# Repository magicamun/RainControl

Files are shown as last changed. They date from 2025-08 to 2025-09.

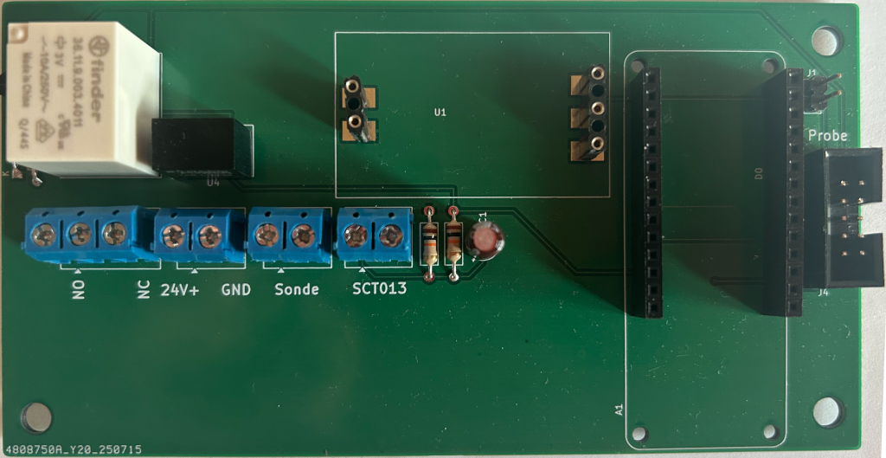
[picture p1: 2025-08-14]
ControllerUnbestückt.png

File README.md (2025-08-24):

# RainControl
Füllstandsmessung einer Zisterne, (Über-)steuerung des Schwimmerschalters der Regenwasserpumpe in Abhängigkeit des Füllstands. 
Messung Strom, Verbrauch der Pumpe, Ableitung an/aus. Anbindung an einen MQTT-Broker zur Werteerfassung und Steuerung

Das Projekt basiert auf der Arbeit aus diesem Repo:

https://github.com/Eisbaeeer/Arduino.Ethernet.Zisterne

Der Nano war aber am Limit was den Speicherplatz angeht und selbst kleinste Optimierungen führten zu zu großen Images oder liefen im Betrieb instabil,
daher habe ich das Projekt auf anderer Hardware aufgesetzt. Zugegeben - das ist jetzt deutlich teurer aber macht so auch mehr Spaß (finde ich).
Ich benötige mangels stabilem WLAN im Technikraum Ethernet - daher das Shield.

Hardware:
  [Arduino MKR Zero](https://store.arduino.cc/collections/mkr-family/products/arduino-mkr-zero-i2s-bus-sd-for-sound-music-digital-audio-data) 
  
  [MKR Ethernet-Shield](https://store.arduino.cc/collections/mkr-family/products/arduino-mkr-eth-shield) - Zur Anbindung an eine Hausatomation, bzw. an einen MQTT-Broker (IOBroker)
  
  Pegelsonde zur Messung des Füllstands mittels Druck - Voraussetzung zur korrekten Füllstandsermittlung ist ein Höhensymmetrisches Volumen (aufrecht stehender Zylinder, Quader), Liegende Zylinderformen sind nicht geeignet. Z.B. so eine hier:
  
  [Füllstandssensor Pegelsensor Drucksensor Wasserstandsensor 4-20mA 0-5m DE](https://www.ebay.de/itm/177255784278?itemid=177255784278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)
  
  [Stromsensor SCT013 - 5A, 1V](https://www.amazon.de/HUABAN-Nicht-invasiver-Split-Core-Stromwandlersensor/dp/B089FNQ5GX?th=1)

  [Steckernetzteil 24V DC](https://www.conrad.de/de/p/dehner-elektronik-saw-30-240-1000g-steckernetzteil-festspannung-24-v-dc-1000-ma-24-w-1549855.html)

Bauteile für die Schaltung, Platine
  
  Controller
  - [Spannungswandler TSR-1 2433 (Wandlung Eingangsspannung 24V auf 3,3V](https://www.conrad.de/de/p/tracopower-tsr-1-2433-dc-dc-wandler-print-24-v-dc-3-3-v-dc-1-a-75-w-anzahl-ausgaenge-1-x-inhalt-1-st-156671.html) zur Versorgung der Schaltung mit 3,3V
  - [Strom/Spannungswandler](https://de.aliexpress.com/item/1005001604138590.html) zur Wandlung des Stroms der Sonde in Spannung inkl. Kalibrierung von 0-Punkt und Maximum
  - [Relais Finder 36.11 Schaltspannung 3V](https://www.conrad.de/de/p/finder-36-11-9-003-4011-printrelais-3-v-dc-10-a-1-wechsler-1-st-3323202.html)
  - [Steckerleisten 14 polig](https://www.conrad.de/de/p/econ-connect-buchsenleiste-standard-anzahl-reihen-1-polzahl-je-reihe-14-blg1x14-1-st-1492306.html)
  - [Transistor BC337](https://www.conrad.de/de/p/diotec-transistor-bjt-diskret-bc337-25-to-92-anzahl-kanaele-1-npn-155900.html) zur Schaltung von Relais und LED
  - D1 [Diode (1N 4148)](https://www.conrad.de/de/p/diotec-ultraschnelle-si-diode-1n4148-sod-27-75-v-150-ma-162280.html)
  - R1 [1x Widerstand 330 Ohm](https://www.conrad.de/de/p/yageo-cfr25j330rh-cfr-25jt-52-330r-kohleschicht-widerstand-330-axial-bedrahtet-0207-0-25-w-5-1-st-1417730.html)
  - R2, R3 [2x Widerstand 10k Ohm](https://www.conrad.de/de/p/yageo-cfr25j10kh-cfr-25jt-52-10k-kohleschicht-widerstand-10-k-axial-bedrahtet-0207-0-25-w-5-1-st-1417697.html)
  - [10uF Elko](https://www.conrad.de/de/p/frolyt-e-rf3058-elektrolyt-kondensator-radial-bedrahtet-2-5-mm-10-f-16-v-20-o-x-l-5-mm-x-12-mm-1-st-3046377.html)
  - 3 x [Schraubklemmblock 2 polig](https://www.conrad.de/de/p/deca-1216197-schraubklemmblock-1-50-mm-polzahl-3-blau-1-st-1216197.html) (Sonde Zisterne, Spannungsversorgung 24V, Stromsensor SCT 013)
  - 1 x [Schraubklemmblock 3-polig](https://www.conrad.de/de/p/deca-1282826-schraubklemmblock-1-50-mm-polzahl-2-blau-1-st-1282826.html) (Umschaltung Regenwasserpumpe, Übersteuerung Schwimmerschaltung - ACHTUNG - 230V)
  
  Displaypanel
  - R1 [1x Widerstand 390 Ohm](https://www.conrad.de/de/p/yageo-mf0207f390rh-mf0207fte52-390r-metallschicht-widerstand-390-axial-bedrahtet-0207-0-6-w-1-1-st-1417596.html)
  - [LED - Rot, 3mm](https://www.conrad.de/de/p/quadrios-2111o155-led-bedrahtet-rot-rund-3-mm-700-mcd-30-20-ma-2-v-2583896.html)
  - [2 Taster (Reset und Mode)](https://www.conrad.de/de/p/weltron-t604-t604-drucktaster-24-v-dc-0-05-a-1-x-aus-ein-tastend-l-x-b-x-h-6-x-6-x-9-5-mm-1-st-700479.html)
  Display
  - [2,42" 128X64-OLED-Anzeigemodul SPI - 2.42 Zoll OLED Bildschirm kompatibel mit Arduino UNO R3 - Weiße Schrift OLED :](https://www.az-delivery.de/products/oled-2-4-white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)

  Zur Verbindung von Controllerplatine mit der Displayplatine:
  
  2 x [Wannenstecker 8polig](https://www.conrad.de/de/p/bkl-electronic-10120552-stiftleiste-ohne-auswurfhebel-rastermass-2-54-mm-polzahl-gesamt-8-anzahl-reihen-2-1-st-741552.html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)
  
  2 x [Pfostensteckverbinder mit Zugentlastung](https://www.conrad.de/de/p/tru-components-1580952-pfosten-steckverbinder-mit-zugentlastung-rastermass-2-54-mm-polzahl-gesamt-8-anzahl-reihen-2-1-1580952.html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)
  
  1 x [Flachbandkabel 8 polig](https://www.conrad.de/de/p/econ-connect-28awg8gr-flachbandkabel-rastermass-1-27-mm-8-x-0-08-mm-grau-30-50-m-1656444.html)

  Sonstiges Material:
  - Bopla Gehäuse](https://www.conrad.de/de/p/bopla-euromas-m-231-02231000-industrie-gehaeuse-160-x-80-x-85-polycarbonat-lichtgrau-ral-7035-1-st-531785.html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)
  - [Passende Einbaubuchse für das Netzteil](https://www.conrad.de/de/p/cliff-scd-026-niedervolt-steckverbinder-buchse-einbau-vertikal-5-5-mm-2-1-mm-1-st-735640.html)
  - [Einbaubuchse für Klinkenstecker vom SCT013](https://www.conrad.de/de/p/tru-components-718574-klinken-steckverbinder-3-5-mm-buchse-einbau-vertikal-polzahl-3-stereo-schwarz-1-st-1564526.html)
    
Das Platinenlyout wurde mit KiCad in 2 Projekten erstellt - eines für das Display, eines für den Controller.

Funktionsweise technisch:

Füllstandsmessung:
  Die Sonde wird mit 24V betrieben und da bietet sich ein Netzteil handelsüblich an und eine Spannungswandlung (TSR-1 2433) von den 24V DC auf 3,3V für den Rest der Schaltung (Arduino MKR Zero, Relais, Display).
  Die Sonde liefert einen Strom in Abhängigkeit vom Druck (Füllstandshöhe). Der Wandler macht aus dem Strom eine Ausgangsspannung von 0 bis Vmax (3,3V).
  Diese Spannung wird am A0 (AnalogInput 0) des Arduino erfasst und in einen Füllstand umgerechnet - der Füllstand (Volumen) ist proportional zum gemessenen Wert an A0.
  Voraussetzung ist ein Behälter, dessen Füllstand (Volumen) sich linear proportional zum Druck verhält (Senkrechter Zylinder).
  
  Der Wandler für den Messwert an A0 muss vor Inbetriebnahme des Systems kalibiriert werden.
  ACHTUNG: Die Kalibrierung muss im ersten Schritt grob ohne angeschlossenen Arduino erfolgen um Beschädigungen durch Überspannung am Eingang des Arduino zu vermeiden.
  -> Siehe Kalibrierung und Inbetriebnahme.
  
  In Abhängigkeit von der gemessenen Füllhöhe und zwei einzustellenden Werten (LimitLow, LimitHigh) schaltet der Arduino das Relais sowie eine LED über PIN D14 an oder aus.
  Damit bei unterem Schwellwert / Minimum nicht sofort bei erneutem überschreiten (Nachlauf Regen) wieder zurück geschaltet wird, gibt es einen weiteren Wert (Oberer Schwellwert),
  der erreicht werden muss, damkt zurück auf Zisterne geschaltet wird.

Strom, Pumpe an oder aus:
  Über den Stromsensor SCT013 kann der Zustand der Pumpe (Regenwassernutzung) abgefragt werden, ohne in die Anlage eingreifen zu müssen.
  Dazu wird der Stromsensor unter der Beachtung der Stromflussrichtung um die Phase (nur die Phase) zur Pumpe gelegt.
  Am Ausgang des Sensors wird über Induktion eine Wechselspannung abgegeben. Dabei sind die Werte des Sensors zur korrekten Berechnung des Stroms und der Leistung in der Software einzustellen.
   Wichtig ist eine korrekte Dimensionierung des Sensors - es gibt unterschiedliche Typen. Für eine möglichst feine Auflösung ist der Messbereich (Ampere) des Sensors möglichst klein zu wählen, 
   aber groß genug, dass bei Vollast der Pumpe der Wert der Leistung ausreicht. Der hier benutzte Sensor misst bis 5A -> 1,1kw. Meine Pumpe hat 800 Watt Leistungsaufnahme.
   Gleichzeitig soll der Sensor möglichst große Spannungswerte am Ausgang produzieren, damit die Auflösung des Wertes möglichst fein/genau ist.
   Es gibt die Sensoren mit 0,33V und 1V Ausgangsspannung -> ich nutze hier 1V. Da die Spannung eine Wechselspannung ist, wird über den Spannungsteiler am Sensor die Wechselspannung um +1,65V angehoben.
   Der analoge Wert an A1 wird in einen Wert für den Stromverbrauch umgerechnt. Dazu ist es wichtig, den Messbereich des Sensors, die Ausgangsspannung des Sensors und den Referenzwert am Arduino (Zero 3,3V)
   zu kennen und in der Software einzustellen.

Am Pin D13 ist ein Taster von der Displayplatine angeschlossen, mit dem der Betriebsmodus der Steuerung manuell gesetzt werden kann:
  - Auto - Der Arduino übernimmt die Ventilsteuerung (Relais und Ansteuerung Schwimmerschalter der Pumpe) in abhängigkeit des Füllstandes
  -   Füllstand < LimitLow -> Relais auf "Hauswasser"
  -   Füllstand > LimitHigh -> Relais auf "Zisterne"
  -   Wenn der Füllstand kleiner als LimitLow war und immernoch kleiner als LimitHigh ist -> Ventil auf Hauswasser
  - Manuell Zisterne -> Relais auf "Zisterne"
  - Manuell Hauswasser -> Relais auf "Hauswasser"

  Per Tasterdruck wird zyklisch durch die Betriuebsmodi geschaltet, wobei die tatsächliche Umschaltung erst nach 10Sekunden ohne erneute Tasterbetätigung erfolgt

Das Display zeigt Datum, Uhrzeit, Füllstand und Betriebsmodus an

Mit dem an RST angeschlossenen Taster lässt sich der Controller resetten.

Ventilsteuerung generell:
Der Controller misst den Füllstand und (kann) in Abhängigkeit davon einen Schwimmerschalter für handelsübliche Zisternenpumpen ersetzen. Dazu ist die Steuerung der Pumpe auf "Automatik" zu stellen
und statt des Schwimmerschalters ein 230V - Kabel vom Anschluss des Schwimmerschalters zum Controller (3 - polige Klemme) zu führen.
Am Schraubklemmenblock 3 polig ist in jedem der mittlere Anschluss zu belegen und dann entweder NO (Normally open) oder NC (normally connected) - sonst schaltet am Ventil der Regenwasserpump nichts.

Funktionsweise Software:

Sämtliche Systemzustände werden bei Veränderung alle Sekunde an einen MQTT-Broker gesendet, spätestens alle 30 Sekunden auch unverändert. Das System führt folgende Werte:

- Booted     -> Boot-Zeitpunkt
- Timestamp  (Datum, Uhrzeit)
- Uptime     -> Zeit seit l. Boot/Neustart
- Mode       (0 = Zisterne, 1 = Hauswasser, 2 = Auto) -> Betriebsmodus
- Modus      -> Modus als Text
- Valve      (0 = Zisterne, 1 = Hauswasser) -> Ventilstellung
- Ventil     -> Ventilstellung als Text ("Zisterne", "Hauswasser")
- Reason     -> Grund für Ventilstellung (0 = "Manuell", 1 = "Zisterne voll", 2 = "Zisterne leer")
- Reasontext -> Reason als Text
- AnalogMin  -> Mindestwert, den die Sonde liefern muss, damit Sonde als vorhanden erkannt wird
- AnalogMax  -> Maximaler analoger Wert an A0 für volle Zisterne
- Analog     (0-1023) -> Analoger Messwert der Pegelsonde (0-1023)
- Liter      -> Füllung in Liter
- Prozent    -> Füllstand in %
- LimitLow   -> Unterer Schwellwert in Liter
- LimitHigh  -> Oberer Schwellwert in Liter
- LiterMin   -> Restfüllstand bei "leer" - unterer Grenzwert -> AnalogMin.
- LiterMax   -> maximales Füllvolumen wird benötigt zur Umrechnung des analogen Wertes in Liter (Analog = LiterMax / AnalogMax)
- StatusSonde-> Ist eine Sonde korrekt angeschlosen (Wenn der Analoge Wert unter einem Minimum liegt, dann ist davon auszugehen, dass die Sonde nicht korrekt angeschlossen ist
- HyaRain    -> Pumpe läuft (ON), oder nicht (OFF)
- Current    -> Stromverbrauch in Ampere
- Power      -> Watt (Volt * Leistung pro Sekunde
- KWh        -> KLilowattstunden

Es gilt:
LiterMin <= LimitLow <= LimitHigh <= LiterMax
Bei mir mit 6500l Zisterne und Restmenge von knapp 500l: 
LiterMin = 500, LimitLow = 600, LimitHigh = 1000, LiterMax = 6500. Bei unterschreiten von 600l schaltet das Relais auf Hauswassernachspeisung,
sobald wieder mehr als 1000l in der Zisterne sind, wird zurück auf Zisterne geschaltet.

Per MQTT kann der Controller aber auch gesteuert werden:
 - cmd/Mode [0,1,2,Hauswasser,Zisterne,Auto] -> Es kann der Modus umgestellt werden (nicht nur per Taster)
 - cmd/Limit [low|high]=<Number> -> Einstellen der Schwellwerte 
 - cmd/Calibrate [analogmin|analogmax|litermax]=<number> -> Einstellen der Kalibrierung in der Software nach dem die Sonde und der Wandler kalibriert wurden

Bei eingelegter SD-Card werden die Daten über einen Reset hinaus auf der SD-Card gespeichert und nach Neustart gelesen.
Wenn man darauf verzichtet die Werte nach dem Aufspielen der Software und der Einstellung in der Software zu verändern ist eine SD-Card nicht nötig

Aufbau, Inbetriebnahme
1. Platinenlayout, Produktion der Platinen
  Im Repository sind in den Unterordnern Controller und Displaypanel je ein KiCad-Projekt mit dem Schema und dem Platinenlayout - wer mag, kann damit andere Platinenformate erzeugen
  oder aber die Schaltung anpassen.
  Die zwei Zip-Archive im Hauptverzeichnis enthalten die Gerberdateien um PCB's produzieren zu lassen. [JLCPCB](https://jlcpcb.com) hat mir gute Dienste geleistet. Der Preis für jeweils 5 Stück (kleinste Einheit) Controler und 
  Display liegt bei 13.50$US - zzgl Versand, Zoll ist man dann bei knapp 30$. Lieferzeit etwa 1 Woche (je nach Zollabfertigung und lokalem Shipment)

2. Aufbau der Platine
  Die Platinen mit den Bauteilen bestücken. Dabei mit den flachen anfangen (Widerstände, Diode, Transistor), dann Buchsenleisten, Schraubklemmenblöcke, Relais, Spannungswandler

  Nach dem Zusammenbau, der Bestückung der Platine erfolgt schrittweise die Inbetriebnahme - noch ohne Arduino und ohne den Strom/Spannungswandler.
  Buchsenleisten sind nützlich für den Arduino (quasi ein muss) und für den Strom-/Spannungswandler. 
  Den Strom/Spannungswandler befreie ich von den Schraubklemmen (auslöten) und ersetze die durch Stiftleisten - einfacher Tausch.
  Dazu bekommt die Platine je Gegenstück eine Buchsenleiste 2 polig und 3 polig mit 5er Raster.

  Bei der Displayplatine darauf achten, dass der Wannenstecker auf die Rückseite kommt und die Polung korrekt ist - siehe Bilder

3. Prüfung der Spannungen
   An Pin 3 des Strom/Spannungswandlers müssen 24V anliegen (auf dem Board rechte Buchsenleiste oberer Pin/Buchse)
   Am Schraubklemmenblock für die Sonde müssen 24V anliegen
   Am Pin 3 der Stiftleiste für den Arduino müssen gegenüber GND (Pin 4) 3,3Volt anliegen

3. Einstellen des Strom/Spannungswandlers (idealerweise bei voller Zisterne)
   Erster Durchgang des Einstellens OHNE Arduino
      Zum Einstellen des Stromspannungswandlers wird selbiger in die Buchsenleisten gesteckt. Ebenso wird an der Stiftleiste "Probe" ein Multimeter zur Spannungsmessung angeschlossen.
      Ohne Sonde liefert das Multimeter dann 0V. Dann wird die Sonde angeschlossen und noch nicht in die Zisterne herabgelasse. Es erfolgt die Nullpunkteinstellung für "leer".
      Mit dem linken Poti dreht man jetzt solange nach links (kleiner) oder nach rechts (größer), bis die gemessene Spannung verlässlich nah an 0V liegt aber eben noch größer als 0V ist.
      Jetzt kann die Sonde in die Zisterne gelassen werden - so tief wie möglich. Zur korrekten Kalibrierung des Maximalwertes ist es am einfachsten den maximalen Füllstand auch zur Einstellung
      der maximalen Spannung zu nutzen. Dazu dreht man jetzt am rechten Poti des Wandlers (links kleiner, rechts größer) bis die gemessene Spannung nah bei 3,3V ist. Es empfiehlt sich etwas "Luft" zu lassen.
   Zweiter Durchgang mit Arduino - die Werte sind verändert, die Vorgehensweise ist die gleiche
      Wichtig ist jetzt, dass jetzt die Analogen Messwerte angeschaut werden.
      Messwert 1 "Sonde angeschlossen, aber nicht unter Druck" -> Dies wird mit dem Poti links auf einen möglichst kleinen aber stabil kleinen Wert über Null eingestellt (bei mir 50).
      Dieser Wert wird in der Software im #DEFINE ANALOG_MIN abgelegt.
      Messwert 2 "Sonde angeschlossen und Maximaler Füllstand der Zisterne und Sonde am tiefsten Punkt (maximaler Druck)
      Den Messwert stellen wir mit dem rechten Poti so ein, dass er möglichst groß ist (nah an 1023), aber noch etwas Luft ist, falls die Zisterne mal "übervoll" ist - Mehr Zulauf als Ablauf (kommt schonmal vor bei mir)
      Den Wert dann in #DEFINE ANALOG_MAX ablegen.
      Die Defines für LITER_MIN mit einem Wert für die Restmenge in der Zisterne bevor die Pumpe auf Störung laufen würde (bei mir sind dann noch 15cm in der Zisterne drin und damit rund 470 Liter.
      LITER_MAX einstellen mit dem maximalen regulären Füllvolumen der Zisterne.

   Wenn die Zisterne nicht voll ist, sollte man abschätzen können, wie voll (in Prozent) sie ist, man kann dann ausgehend vom Zielwert bei "Zisterne Voll" nah bei 3,3V und
   dem unteren Messwert für "leer" den Spannungswert, den man jetzt messen möchte im Dreisatz ableiten und dann einstellen am Poti.
4. Aufspielen der Software auf den Arduino
5. Board stromlos machen / Spannungsversorgung trennen
6. Aufstecken des Arduino und des Ethernet-Shields auf die Buchsenleisten 14 polig
7. Verbinden des Displays mit dem Controller (Wenn das Display NICHT angeschlossen ist, dann wird der Arduino NICHTS tun.)
8. Netzteil anschließen
9. Der Arduino bootet und auf dem Display werden die Daten angezeigt
10. Die Daten werden zyklisch an den MQTT-Broker verteilt (Bei Änderungen sekündlich, ansonsten alle 30 Sekunden)
11. Prüfung der Messwerte am Broker
12. Es empfiehlt sich, dass nach ein paar Wochen Betrieb und Leer, Voll-Zyklen nochmal die Messwerte der Kalibrierung geprüft werden und notfalls nochmal in der Software neu eingestellt werden - entweder per MQTT oder "hart" per Software

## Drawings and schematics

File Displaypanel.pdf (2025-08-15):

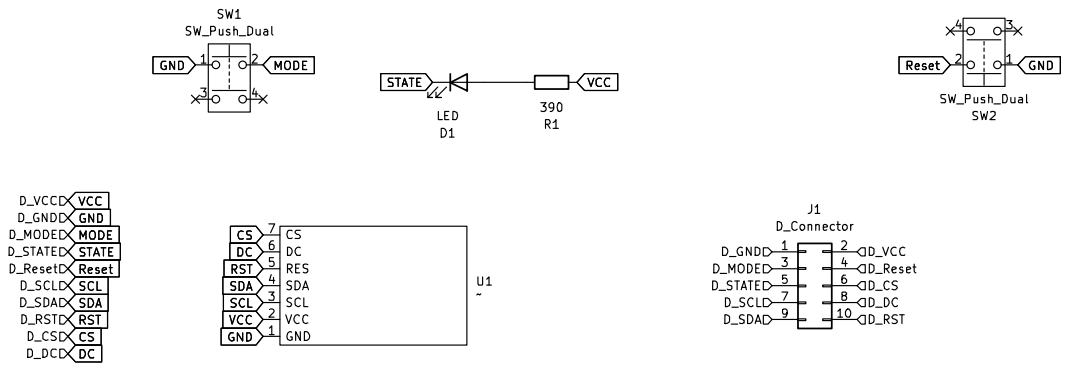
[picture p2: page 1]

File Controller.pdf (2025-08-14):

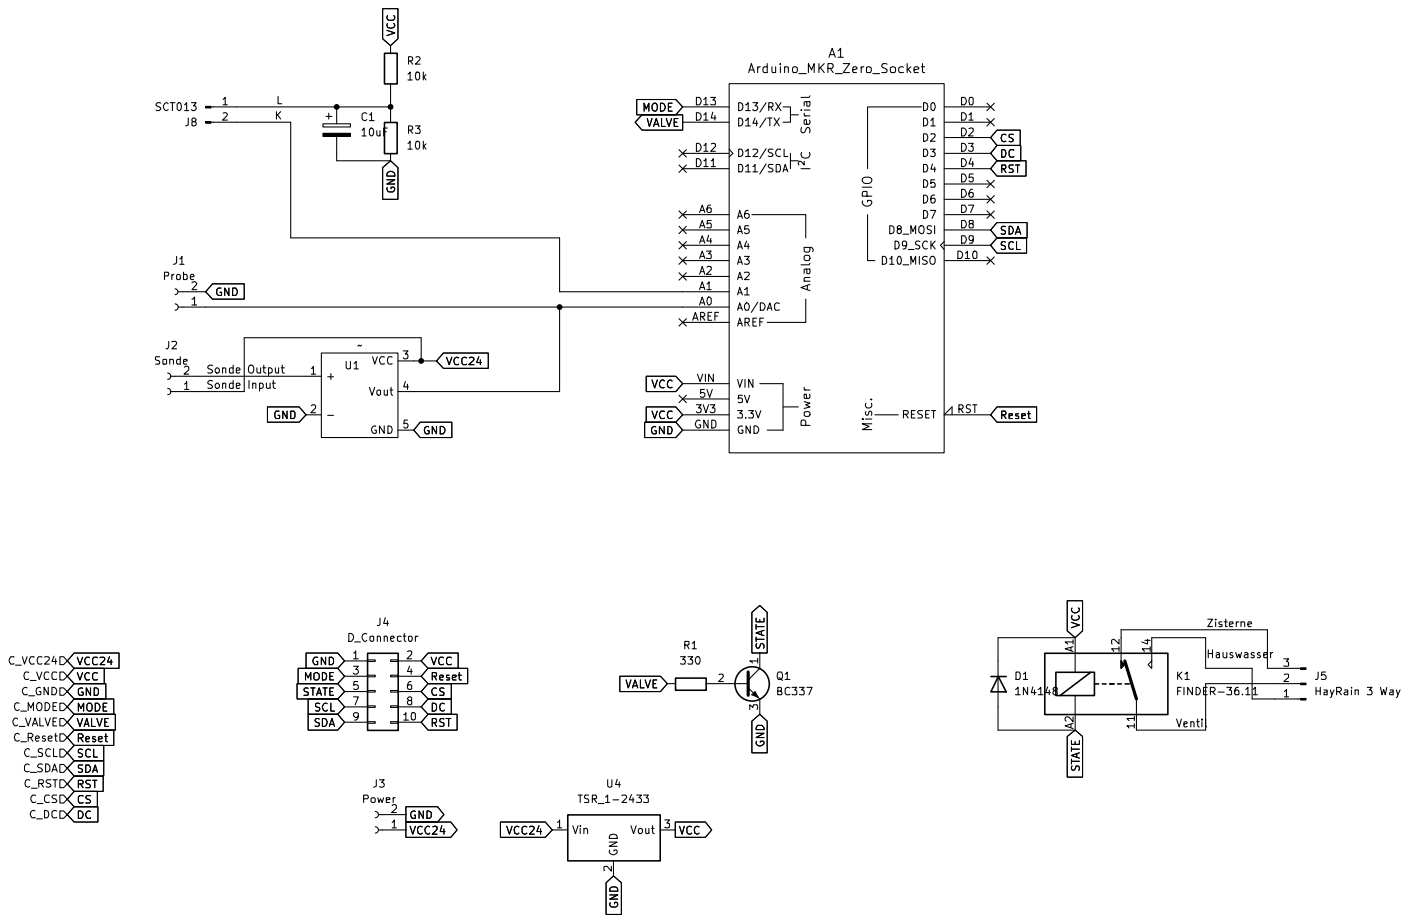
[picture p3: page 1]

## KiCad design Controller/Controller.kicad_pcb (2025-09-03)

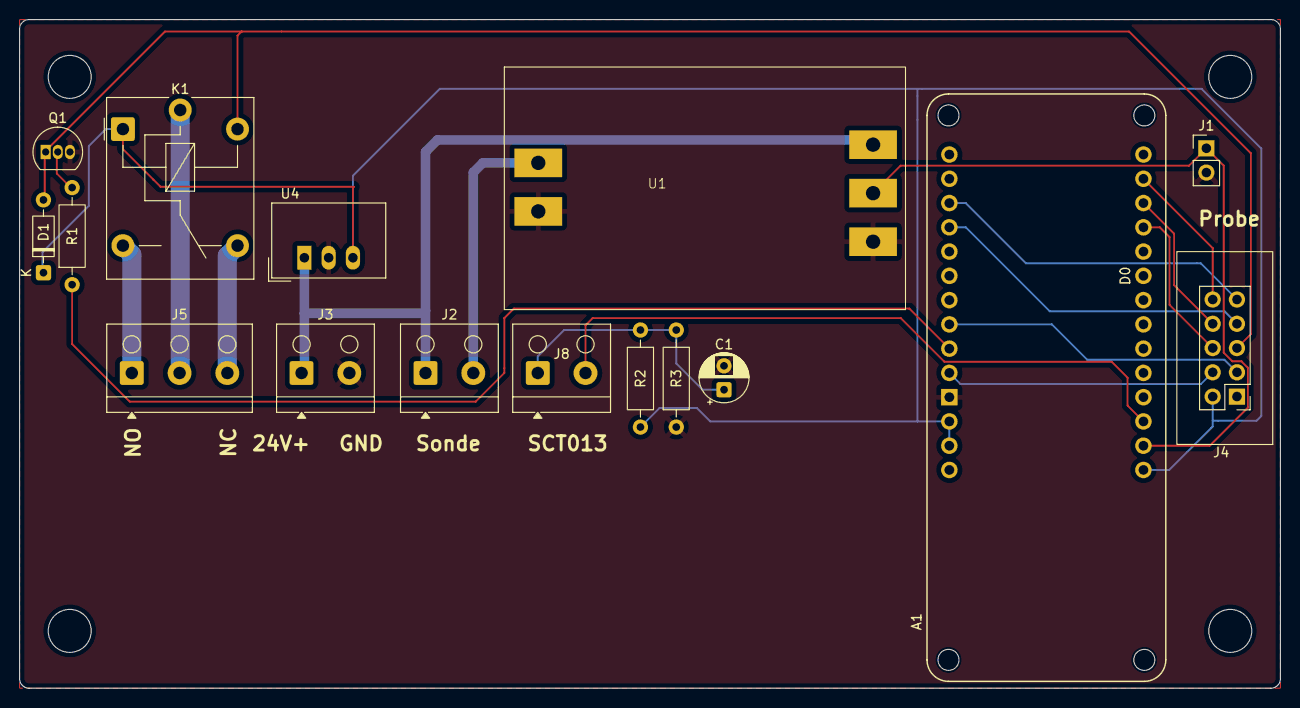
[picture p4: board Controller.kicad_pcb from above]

Board: 2 copper layers, 132.0 x 70.0 mm, 16 parts (0 on the bottom side), 20 nets.

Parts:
A1: Arduino_MKR_Zero_Socket
C1: 10uF; CP_Radial_D5.0mm_P2.50mm
D1: 1N4148; D_DO-35_SOD27_P7.62mm_Horizontal
J1: Probe; PinHeader_1x02_P2.54mm_Vertical
J2: Sonde; TerminalBlock_RND_205-00001_1x02_P5.00mm_Horizontal
J3: Power; TerminalBlock_RND_205-00001_1x02_P5.00mm_Horizontal
J4: D_Connector; WSL 10G
J5: HayRain 3 Way; TerminalBlock_RND_205-00002_1x03_P5.00mm_Horizontal
J8: SCT013; TerminalBlock_RND_205-00001_1x02_P5.00mm_Horizontal
K1: FINDER-36.11; Relay_SPDT_Finder_36.11
Q1: BC337; TO-92_Inline
R1: 330; R_Axial_DIN0207_L6.3mm_D2.5mm_P10.16mm_Horizontal
R2, R3: 10k; R_Axial_DIN0207_L6.3mm_D2.5mm_P10.16mm_Horizontal
U1: Konverter
U4: TSR_1-2433; Converter_DCDC_TRACO_TSR-1_THT

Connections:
/Hauswasser: J5.1, K1.14
/K: A1.A1, J8.2
/L: C1.1, J8.1, R2.1, R3.2
/Sonde Output: J2.2, U1.1 (+)
/Ventil: J5.2, K1.11
/Zisterne: J5.3, K1.12
CS: A1.D2, J4.6
DC: A1.D3, J4.8
GND: A1.GND, C1.2, J1.2, J3.2, J4.1, Q1.3 (E), R3.1, U1.2 (-), U1.5 (GND), U4.2 (GND)
MODE: A1.D13 (D13/RX), J4.3
unnamed: A1.A0 (A0/DAC), J1.1, U1.4 (Vout)
unnamed: Q1.2 (B), R1.2
RST: A1.D4, J4.10
Reset: A1.RST (RESET), J4.4
SCL: A1.D9 (D9_SCK), J4.7
SDA: A1.D8 (D8_MOSI), J4.9
STATE: D1.2 (A), J4.5, K1.A2, Q1.1 (C)
VALVE: A1.D14 (D14/TX), R1.1
VCC: A1.3V3 (3.3V), A1.AREF, A1.VIN, D1.1 (K), J4.2, K1.A1, R2.2, U4.3 (Vout)
VCC24: J2.1, J3.1, U1.3 (VCC), U4.1 (Vin)

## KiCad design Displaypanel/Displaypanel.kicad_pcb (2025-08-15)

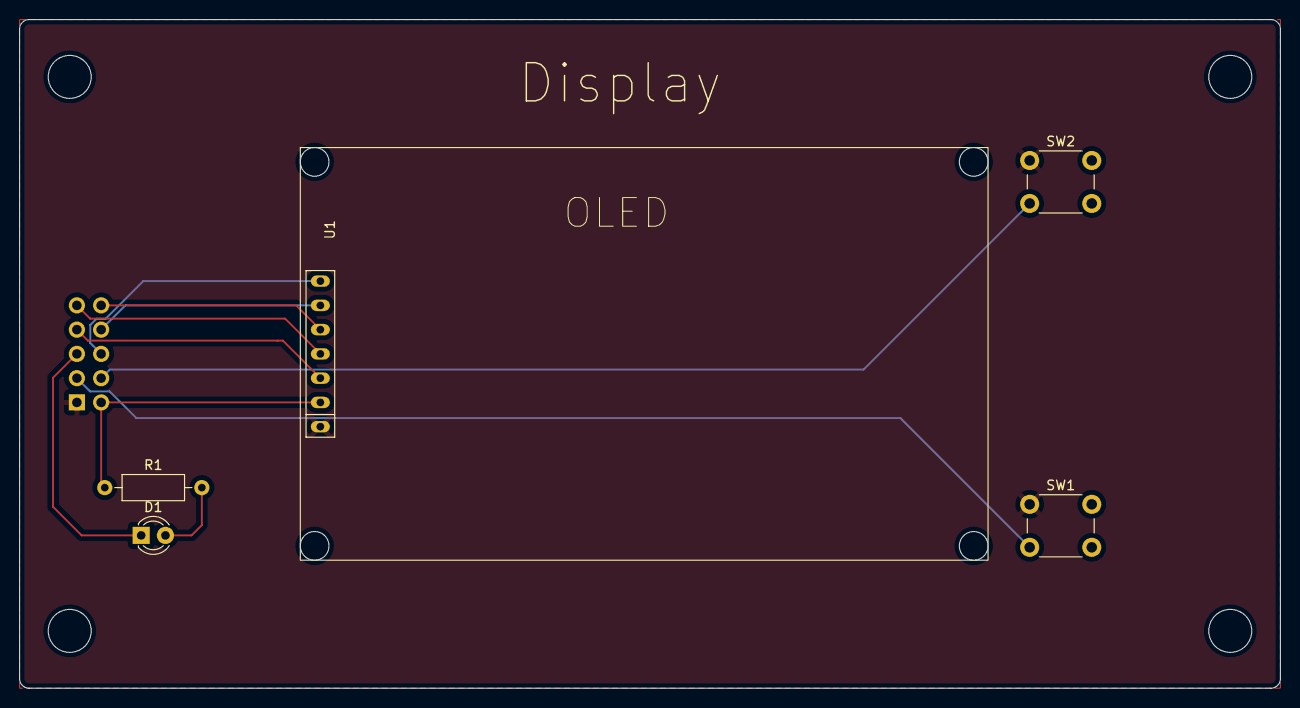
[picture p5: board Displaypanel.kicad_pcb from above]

Board: 2 copper layers, 132.0 x 70.0 mm, 6 parts (1 on the bottom side), 11 nets.

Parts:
D1: LED; LED_D3.0mm_Clear
J1: D_Connector; WSL 10G
R1: 390; R_Axial_DIN0207_L6.3mm_D2.5mm_P10.16mm_Horizontal
SW1, SW2: SW_Push_Dual; SW_PUSH_6mm_H4.3mm
U1: OLED 128x64 SPI

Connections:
CS: J1.6, U1.7 (CS)
DC: J1.8, U1.6 (DC)
GND: J1.1, SW1.1, SW2.1, U1.1 (GND)
MODE: J1.3, SW1.2
unnamed: D1.2 (A), R1.2
RST: J1.10, U1.5 (RES)
Reset: J1.4, SW2.2
SCL: J1.7, U1.3 (SCL)
SDA: J1.9, U1.4 (SDA)
STATE: D1.1 (K), J1.5
VCC: J1.2, R1.1, U1.2 (VCC)

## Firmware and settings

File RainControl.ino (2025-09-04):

#include <Arduino.h>
#include <avr/dtostrf.h>
#include <PubSubClient.h>
#include <Time.h>
#include <Ethernet.h>
EthernetClient ethClient;

#include <EthernetUdp.h>
EthernetUDP Udp;

#include <MyNTP.h>
MyNTP ntp(Udp);

#include <SD.h>
#include <U8g2lib.h>
U8G2_SSD1309_128X64_NONAME2_F_4W_HW_SPI u8g2(U8G2_R0, /* cs=*/ 2, /* dc=*/ 3, /* reset=*/ 4);

#ifdef U8X8_HAVE_HW_SPI
#include <SPI.h>
#endif
#ifdef U8X8_HAVE_HW_I2C
#include <Wire.h>
#endif

/* ---------------------------- allgemeine Settings ----------------------------- */
#define VERSION "RainControl V1.0"

// For Debugging with no Display connected, comment out for real-world
#define HAS_DISPLAY
// Minimize Serial Output
// #define DEBUG
// ##############################################################################################################################
// ---- HIER die Initialen Einstellungen vornehmen, die Werte sind über MQTT anpassbar
// ##############################################################################################################################
// Hier die maximale Füllmenge des Behälters angeben. Dies gilt nur für symmetrische Behälter.
// Deckelung bei 100%
// keine Deckelung bei "Übervoll", sondern Max-Wert ist maximal nutzbarer (Überlauf)
// Analoger Wert bei maximalem Füllstand (wird alle 30 Sekungen auf dem LCD angezeigt oder in der seriellen Konsole mit 9600 Baud.
// Maxwerte mit 100% - Deckelung
// const int analog_max = 972;
// const int analog_min = 50;
// Maxwerte ohne Deckelung bei 100%
#include "SAMD_AnalogCorrection.h"

#define ADC_RESOLUTION_BITS  12 // do not change. This library only supports 12 bit resolution.
#define ADC_RANGE            (1 << ADC_RESOLUTION_BITS)
#define ADC_TOP_VALUE        (ADC_RANGE - 1)

#define ANALOG_MIN 200      // Analoger Messwert A0 (alles was kleiner ist, wird als "Sonde defekt oder nicht angeschlossen" gewertet)
#define ANALOG_MAX 4000     // Analoger Messwert A0 (bei 100% Füllgrad)

#define LITER_MIN 600       // Restfüllmenge bei Minimum (wird nur erreicht, wenn Übersteuert wird / wurde) - der Saugschlauch wird in der Regel nicht restlos leer pumpen
#define LITER_MAX 6500      // Maximale Füllmenge
#define LIMIT_LOW 700       // Liter
#define LIMIT_HIGH 1000     // Liter

#define MODE_PIN 13
#define MODE_ZISTERNE 0
#define MODE_HAUSWASSER 1
#define MODE_AUTO 2
#define MODE_COUNT 10
bool setmode = false;
char *modes[] = {"Zisterne", "Hauswasser", "Auto"};
int mode_count = MODE_COUNT;

int old_mode = MODE_AUTO;
int pin_stat;
int old_stat;

#define VALVE_PIN 14
#define VALVE_ZISTERNE LOW
#define VALVE_HAUSWASSER HIGH
int new_valve = VALVE_ZISTERNE;
char *valves[] = {"Zisterne", "Hauswasser"};
char *reasons[] = {"Manuell", "Zisterne voll", "Zisterne leer"};

// Status HyaRain (Currently unused)
#define ERROR_PIN 1
char *hyaraintext[] = {"Off", "On", "Failure", "Invalid"};

// No more delay
unsigned long pubMillis;        // MQTT - Refresh
unsigned long updateMillis;     
#define SEKUNDE 1000  // one second

unsigned long pinMillis;
unsigned long lastMillis = 0;

char uptime[20];
char *up = &uptime[0];

char buf[255];
/* ---------------------------- Topics -----------------------------------
   Basisklassen für ein MQTT - Topic. Die Klasse speichert ein Topic bestehend aus
   dem Topic-Namen, einem Wert des Topics, (INteger, float, double, bool oder char*
   sowie den Änderungszustand des Topics.
   Basisklasse TopicBase
   Die Klasse Topic überlagert TopicBase und implementiert die Methoden zur Kommunikation mit
   dem Broker oder zum setzen, lesen von Werten.
   Die Klasse Topic überlagert auch den Operator "=" - Das Topic lässt sich benutzen wie eine Variable.
   ----------------------------------------------------------------------- */
// Ersatz für std::is_same (Arduino-kompatibel)
template<typename A, typename B>
struct is_same_type { static const bool value = false; };

template<typename A>
struct is_same_type<A, A> { static const bool value = true; };

class TopicBase {
    protected:
        const char *name;
        const char *fmt;
        bool changed;
    
    public:
        TopicBase(const char *_name, const char *_fmt = nullptr) : name(_name), fmt(_fmt), changed(true) {};
        virtual ~TopicBase() {};

        const char * getName() const { return name; };
        void setFormat(const char *_fmt) { fmt = _fmt; };
        void Changed() {changed = true;};

        // Von abgeleiteten Klassen (Topic) zu Implementieren
        virtual void Publish(PubSubClient *_mqttclient, char * _mqtt_id) = 0;
        virtual char *toString() = 0;
};

// ---------------------------------------------------------
// Hilfsfunktion für time_t → String
// ---------------------------------------------------------
inline void timeToString(const time_t *t, const char* fmt, char* buffer, size_t size) {
    if (!t || !buffer || size == 0) 
        return;

    struct tm *timeinfo = ntp.localTime(*t);

    if (timeinfo) {
        strftime(buffer, size, fmt ? fmt : "%d.%m.%Y %H:%M:%S", timeinfo);
    } else {
        snprintf(buffer, size, "[invalid time]");
    }
}

template <typename Type>
class Topic : public TopicBase {
    private:
        Type data;

    public:
        Topic(const char *_name, Type value, const char *_fmt = nullptr) : TopicBase(_name, _fmt), data(value) { };

        // Zuweisungsoperator überladen
        Topic<Type>& operator=(const Type& value) {
            setData(value);
            return *this;
        }

        // Typ-Konvertierungsoperator (Lesen)
        operator Type() const {
            return getData();
        }
    
        // Getter, Setter
        Type getData() const { return data; }

        void setData(Type value) {
            if (value != data) {
                data = value;
                changed = true;
            }
        };

        char *toString() override {
            static char tostring[64];
            tostring[0] = 0;

            if constexpr (is_same_type<Type, const time_t>::value || is_same_type<Type, time_t>::value) {
                timeToString(&data, fmt, tostring, sizeof(tostring));
                return tostring;
            }
            
            if (fmt) {
                snprintf(tostring, sizeof(tostring), fmt, data);
                return tostring;
            }
            if (is_same_type<Type, int>::value) {
                snprintf(tostring, sizeof(tostring), "%d", data);
            } else if (is_same_type<Type, float>::value || is_same_type<Type, double>::value) {
                snprintf(tostring, sizeof(tostring), "%.3f", data);
            } else if (is_same_type<Type, const char*>::value || is_same_type<Type, char*>::value) {
                snprintf(tostring, sizeof(tostring), "%s", data);
            } else if (is_same_type<Type, const bool>::value || is_same_type<Type, bool>::value) {
                snprintf(tostring, sizeof(tostring), "%s", data ? "true" : "false");
            } else {
                snprintf(tostring, sizeof(tostring), "[unsupported type]");
            }
            return tostring;
        }


        void Publish(PubSubClient *_mqttclient, char * _mqtt_id) override {
            char _t[256];

            sprintf(_t, "%s/%s", _mqtt_id, name);
            if (changed) {
                if (_mqttclient->connected()) {
                    changed = false;
                    _mqttclient->publish(_t, toString());
                }
#ifdef DEBUG
                changed = false;
#endif
                Serial.print(_mqtt_id);
                Serial.print("/");
                Serial.print(name);
                Serial.print(" ");
                Serial.println(toString());
            }
        };
};

/* Definition der Topics zur Speicherung der Daten sowhol hier im Code, als auch in Richtung Broker */

#define TOPIC_LIST                                  \
    X(Timestamp, time_t, 0, "%d.%m.%Y %H:%M:%S")    \
    X(Mode, int, MODE_AUTO, "%d")                   \
    X(Modus, char *, modes[MODE_AUTO], "%s")        \
    X(Valve, int, VALVE_ZISTERNE, "%d")             \
    X(Ventil, char *, valves[VALVE_ZISTERNE], "%s") \
    X(Analog, int, 0, "%d")                         \
    X(Liter, int, 0, "%4d")                         \
    X(LimitLow, int, LIMIT_LOW, "%d")               \
    X(LimitHigh, int, LIMIT_HIGH, "%d")             \
    X(LiterMin, int, LITER_MIN, "%d")               \
    X(LiterMax, int, LITER_MAX, "%d")               \
    X(Prozent, double, 0.0, "%5.1f%%")              \
    X(Uptime, char*, "", "%s")                      \
    X(StatusSonde, bool, true, nullptr)             \
    X(HyaRain, char*, "", "%s")                     \
    X(Booted, time_t, 0, "%d.%m.%Y %H:%M:%S")       \
    X(AnalogMin, int, ANALOG_MIN, "%d")             \
    X(AnalogMax, int, ANALOG_MAX, "%d")             \
    X(Scale, double, 1.0, nullptr)                  \
    X(Ampere, double, 0.0, "%.2f")                  \
    X(Power, double, 0.0, "%.2f")                   \
    X(KWh, double, 0.0, "%.2f")                     \
    X(Reason, int, 0, "%d")                         \
    X(ReasonText, char*, reasons[0], nullptr)


#define X(name, type, init, format)    Topic<type> name(#name, init, format);
TOPIC_LIST
#undef X

#define X(name, type, init, format) &name,
TopicBase* topics[] = { TOPIC_LIST };
#undef X

#define NUM_TOPICS (sizeof(topics) / sizeof(topics[0]))

/* ------------------------------ Analog Input ---------------------------
   Basisklasse zur Behandlung von analogen Inputs
   Instantiiert für einen Analogen Eingang, optional wird ein Offset/Average
   für den Messwert mitgegeben - nützlich für Messwerte, die um einen Mittelpunkt schwanken
   ----------------------------------------------------------------------- */
/* ------------------------------ Analog Input ---------------------- */
class AI {
    protected:
        int pin;
        int count;
        long aggregate;
        long average;
    public:
        AI(int _pin, int _average = 0) {
            pin = _pin; count = 0; aggregate = 0; average = _average;
        };
        // Anzahl Messungen
        int Count() {
            return count;
        };
        // Messwert lesen am Eingang, Aufsummieren, Anzahl Messungen erhöhen und Average mitlaufen lassen (aufaddieren), der Messwert wird als absolute Differenz zum Average/Mittelwert betrachtet
        void Read(int _average = 0) {
            int val = analogRead(pin);
            aggregate += abs(val - _average);
            average += val;
            count++;
        };

        int Aggregate() {
            return aggregate;
        }

        // Wert zurückgeben, dabei die Summe der Messwerte durch die Anzahl teilen
        int Value() {
            if (count > 0 && aggregate > count) {
                return max(aggregate / count - 1, 0);
            } else {
                return 0;
            }
        };

        // Value als Wert im verhältnis zu Max und minimun zurückgeben (integer)
        int Value(int _max, int _min = 0) {
            if (_max > _min) {
                return Value() / ADC_TOP_VALUE * (_max - _min);
            } else {
                return 0;
            }
        }

        // Value als Wert im verhältnis zu Max und minimun zurückgeben (double)
        double Value(double _max, double _min = 0.0) {
            if (_max > _min) {
                return (double) Value() / (double)ADC_TOP_VALUE * (_max - _min);
            } else {
                return 0;
            }
        }
        // Value als Prozentwert zurückgeben (double)
        double Percent() {
            return (double)Value() / (double)ADC_TOP_VALUE * 100.0;
        }

        // Mittelwert der Messungen - nützlich, notwendig für Wechselspannungswerte zur erkennung der Kalibrierung Nullpunkt
        int Average() {
            if (count > 0) {
                return average / count;
            } else {
                return 0;
            }
        };

        // Messreihe neu starten, alle Werte zurücksetzen
        void Restart() {
            aggregate = 0;
            if (count > 0) {
                average = average / count;
            } else {
                average = 0;
            }
            count = 0;
        };
};

/* ------------------------------ Analog Input ---------------------------
   Energy - Klasse für die Messwertermittlung von Werten des Stromsensors SCT013
   die Werte am Eingang A1 sind über den Spannungsteiler an A1 um 1,65V angehoben
   und oszillieren um die Hälfte der ADC_RANGE herum - Mittelpunkt, Average wird mit ADC_RANGE / 2 begonnen
   ----------------------------------------------------------------------- */
class Energy : public AI {
    private:
        double ampmax;  // Maximale Ampere bei maximaler Amplitude -> 1, 5, 10, 30, 100 Amp
        double vmax;    // Maximale Spannung Analogamplitude Signal (muss kleiner Referenzspannung sein) 
        
        double volt;    // Netzspannung
        double vrefmax; // Referenzspannung Arduino (3,3 oder 5V)
        double vrefmin; // Unterer Spannungswert (i.d.R. 0V)

        int imin;       // Integer - Min am Analogen Input -> i.d.R. 0
        int imax;       // Integer - Max am analogen Input -> i.d.R. 1024

        double scale;   // Umrechnungsfaktor
        
        double amp;
        double watt;
        double wattseconds;
        unsigned long wattmillis;

    public:
        Energy(int _pin, double _ampmax, double _vmax, double _volt = 230, double _vrefmax = 3.3, double _vrefmin = 0, int _imax = ADC_RANGE, int _imin = 0) : AI(_pin, ADC_RANGE / 2) {
            ampmax = _ampmax;
            vmax = _vmax;
            volt = _volt;
            vrefmax = _vrefmax;
            vrefmin = _vrefmin;
            imax = _imax;
            imin = _imin;
            wattseconds = 0;
            wattmillis = millis();
            watt = 0;
            // Scale ist der Faktor mit dem der analoge Messwert multipliziert werden muss. Er ergibt sich aus:
            // maximalem Messbereich des Sensors in Ampere , maximaler Referenzspannung (Arduino Zero = 3.3)
            // minimaler Referenzspannung (0.0), dem Maximalen Wert des Analogen Inputs (ADC_MAX_VALUE) dem minimalen Wert (0)
            // und der maximalen Spannung des Sensors SCT013 (1V)
            scale = ampmax * (vrefmax - vrefmin) / (double)(imax - imin) / vmax;
        };
        double Scale() {
            return scale;
        };

        double Amp() {
#ifdef DEBUG
            Serial.print("C: ");
            Serial.print(count);
            Serial.print(", A: ");
            Serial.print(aggregate);
            Serial.print(", S:  ");
            Serial.println(scale);
#endif
            if (count > 0 && aggregate > 2 * count) {
                amp = roundf(max(((double) aggregate / (double)count - 1.0), 0) * scale * 10) / 10;
            } else {
                amp = 0;
            }
            return amp;
        };

        double Volt() {
            return volt;
        };

        double Power() {
            return Volt() * Amp();
        };

        void ResetKwh() {
            wattseconds = 0;
            wattmillis = millis();
            watt = 0;
        };

        double Watt() {
            return watt;
        };

        double Seconds() {
            return wattseconds;
        };

        double KWh() {
            return watt / 3600 / 1000;
        };

        void Restart() {
            if (wattseconds > 0) {
                watt += (Volt() * Amp() / wattseconds);
            }
            wattseconds += ((double) millis() - (double) wattmillis) / 1000;

            aggregate = 0;
            if (count > 0) {
                average = average / count;
            } else {
                average = 0;
            }
            count = 0;
            wattmillis = millis();
        };
};

AI Sonde(A0);                               // Drucksonde Zisterne an A0
Energy sct013(A1, 5.0, 1.0, 230, 3.3, 0, ADC_TOP_VALUE);      // Energiesensor SCT013 - 5A, 1V, 230V Netzspannung, 3.3V VCC Arduino (MKR Zero) an A1
int average = ADC_RANGE / 2;                           // Mittelpunkts-Wert selbstkalibrierend für Stromsensor SCT013

/* ----------------------------- Ethernet ---------------------------- */
// MAC-Addresse bitte anpassen! Sollte auf dem Netzwerkmodul stehen. Ansonsten eine generieren.
byte mac[] = { 0xDE, 0xAD, 0xBE, 0xEF, 0xFE, 0x0C };

// IP Adresse, falls kein DHCP vorhanden ist. Diese Adresse wird nur verwendet, wenn der DHCP-Server nicht erreichbar ist.
IPAddress ip(192, 168,   3,  95);
IPAddress ns(192, 168,   3, 254);
IPAddress gw(192, 168,   3, 254);
IPAddress sn(255, 255, 255,   0);


/* ------------------------------- NTP ------------------------------- */
#define NTPSERVER "pool.ntp.org"
bool ntp_time = false;

#define SECONDS_PER_MINUTE 60
#define SECONDS_PER_HOUR (60 * SECONDS_PER_MINUTE)
#define SECONDS_PER_DAY (24 * SECONDS_PER_HOUR)

/* ---------------------------- SD Card ---------------------------- */

const int chipSelect = SDCARD_SS_PIN;
boolean SDStatus = true;
File SDSettings;
#define SETTINGSFILE "RC.ini"
File SDLogger;
#define LOGFILE "RC.csv"

struct SDData {
    char *id;
    int analogMin;
    int analogMax;
    int literMin;
    int literMax;
    int limitLow;
    int limitHigh;
    double scale;
} sddata = {"RC", ANALOG_MIN, ANALOG_MAX, LITER_MIN, LITER_MAX, LIMIT_LOW, LIMIT_HIGH, 15.0};
char *sdini_format = "%2s;%d;%d;%d;%d;%d;%d;%s;";

/* ----------------------------- MQTT ---------------------------- */
// MQTT definitions
#define MQTT_ID "RainControl"
void MqttCallback(char *topic, byte *payload, unsigned int length);
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
void loop() {
    // put your main code here, to run repeatedly:

    sct013.Read(average);
    Sonde.Read();

    pin_stat = digitalRead(MODE_PIN);
    pinMillis = millis();
    
    if (pin_stat == LOW) {
        if (pinMillis - lastMillis > 200) {
#ifdef DEBUG
            Serial.println("Impuls Low");
#endif
            lastMillis = pinMillis;
            mode_count = MODE_COUNT;
            if (!setmode) {
                setmode = true;
                old_mode = Mode;
#ifdef DEBUG
                sprintf(buf, "Button: Enter Settings-Mode %d (%s)", Mode, Modus);
                Serial.println(buf);
#endif
            } else {
                Mode = Mode - 1;
                if (Mode < 0) {
                    Mode = 2;
                }
                Modus = modes[Mode];
#ifdef DEBUG
                sprintf(buf, "Button: Mode change to %d (%s)", Mode, Modus.toString());
                Serial.println(buf);
#endif
            }
        }
    }


    if ((millis() - pubMillis) > SEND_INTERVAL * 1000) { // Alle 30 Sekunden
        for (int i = 0; i < (sizeof(topics) / sizeof(topics[0])); i++) {
            topics[i]->Changed();
        }
        // SDLogData();
        MqttPublish();
        pubMillis = millis();
    }
    if (millis() - updateMillis >= SEKUNDE) { // Hier eine Sekunde warten
        if (mqttclient.connected()) {
            mqttclient.loop();
        }
        StatusSonde = Analog >= sddata.analogMin;             // Sondenfehler ?
#ifdef DEBUG
        Serial.println("Analogen Wert lesen Sonde");
#endif
        /* Analoger Wert der Sonde geglättet */
        Analog = Sonde.Value();
        // Serial.println("Restart Sonde");
        Sonde.Restart();

        Prozent = (Analog - AnalogMin) * 100 / (AnalogMax - AnalogMin);                                 // Calculate Prozent
        Liter = LiterMin + (Analog - AnalogMin) * (LiterMax - LiterMin) / (AnalogMax - AnalogMin);      // calculate liter

        /* Analoger Wert des Stromsensors geglättet */
#ifdef DEBUG
        Serial.println("Analogen Wert lesen Stromsensor");
#endif
        Ampere = sct013.Amp();
        if (Ampere > 0) {
            HyaRain = "On";
        } else {
            HyaRain = "Off";
        }
        Power = sct013.Power();
        KWh = sct013.KWh();

        average = sct013.Average();
        sct013.Restart();

        if (Ethernet.hardwareStatus() != EthernetNoHardware && Ethernet.linkStatus() == LinkON) {
            ntp.update();

#ifdef DEBUG
            Serial.println("Get NTP-Time Epoch");
#endif
            Timestamp = ntp.epoch();
#ifdef DEBUG
            sprintf(buf, "%s", ntp.formattedTime("%d.%m.%Y %H:%M:%S"));
            Serial.println(buf);
#endif
        }
        
        // ReadAnalog();
        CheckEthernet();
        CalcUptime();

        if (Booted == 0) {
            Booted = Timestamp.getData();
        }

        if (setmode) {
            mode_count--;
            if (mode_count <= 0) {
                old_mode = Mode;
                setmode = false;
            }
        }
        if (!setmode) {
            if (Mode == MODE_ZISTERNE) {
                new_valve = VALVE_ZISTERNE;
                Reason = 0;
            } else if (Mode == MODE_HAUSWASSER) {
                new_valve = VALVE_HAUSWASSER;
                Reason = 0;
            } else if (Mode == MODE_AUTO) {
                if (Liter >= sddata.limitHigh) {
                    new_valve = VALVE_ZISTERNE;
                    Reason = 1;
                }
                if (Liter <= sddata.limitLow) {
                    new_valve = VALVE_HAUSWASSER;
                    Reason = 2;
                }
            }
            ReasonText = reasons[Reason];

            Modus = modes[Mode];
        }
        /*-----------------------------------------------------------
        * Wenn Ventil umzuschalten ist
        */
        if (new_valve != Valve) {
            Valve = new_valve;
            Ventil = valves[Valve];
            digitalWrite(VALVE_PIN, Valve);
#ifdef DEBUG
            sprintf(buf, "Mode: %s, set Valve to %s (%s)", Modus, Ventil, ReasonText);
            Serial.println(buf);
#endif
        }

        // print out to Display
        CDisplay();
        MqttPublish();
        updateMillis = millis();
    }
}

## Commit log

2025-08-14 KICad Controller added
    [Controller.kicad_pcb, Controller.kicad_sch]
2025-08-14 Updated KiCad Controller
    [Controller.kicad_sch]
2025-08-15 Added DisplayPanel
    [Displaypanel.kicad_pcb, Displaypanel.kicad_sch]
2025-08-15 Updated KiCad, Gerber-Files
    [Controller-B_Cu.gbr, Controller-B_Mask.gbr, Controller-B_Paste.gbr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]
2025-08-15 Moved Gerberfiles
2025-08-16 Fixed Output of Topics, Code-Cleanup
    [RainControl.ino]
2025-08-17 Changed Readme, Bumped Version
    Changed version/Revision to 1.0
    Fixed MQTT_ID
    [Controller.kicad_pcb, Controller.kicad_sch]
2025-08-21 Bessere Deklaration der Topics
2025-09-03 Update RainControl.ino
    Set Resolution to 12 Bit, Anpassung des Codes - Nutzung ADC_RESOLUTION_BITS etc, Rundung Ampere auf 0,1
2025-09-03 Footprints updated, AREF to VCC
    Updated Footprints from updatet Libraries and connected AREF to VCC,
    Rerouted
    [Controller.kicad_pcb, Controller.kicad_sch]
2025-09-04 Update RainControl.ino
    Umstellung auf MyNTP-Lib - korrigierte Version für ntp.localTime
    [RainControl.ino]
